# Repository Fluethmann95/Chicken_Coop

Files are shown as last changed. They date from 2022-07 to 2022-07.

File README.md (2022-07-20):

# Hühnerklappensteuerung

- Vollautomatische Steuerung für Stalltüren
- Möglichkeit der Ansteuerung über verschiedene Wege:
	- Am Gerät einstellbarer Zeit für Öffnen und Schließen
	- Helligkeit über externen Sensor
	- Handbetrieb per Drucktaster
- Einstellbare Fahrtzeit in 1/10 Sekunden
- Einstellbare Uhrzeit
- Anschluss für User-Button und Poti
- Diagnose und Konfiguration über LCD und RGB-LED
- 2 Anschlussmöglichkeiten für PNP/NPN Endstops
- Automatische Zeitsynchronisation bei Upload mit PC Zeit
- Update des Codes über SD Karte

##Technische Details
- Arduino MKRZERO µC-Board
- Zeitmessung über DS3231 RTC
- Solar Laderegler mit automatisch geregelter Ladespannung
- PWM Motorausgang mit Strommessung und H-Brücke
- Batteriemanagement

##Aktuelle Konfiguration
- Fahrtdauer 250 s/10
- Öffnen 5:20 Uhr
- Schließen 22:10 Uhr

##Benötigtes Material
- Steuerungsplatine inkl passendem Gehäuse (RND-455 00265)
- Elektromotor 12V mit passendem Getriebe und Seilrolle
- Solarpanel 12V 20Wmax.
- Bleigelbatterie ~10Ah

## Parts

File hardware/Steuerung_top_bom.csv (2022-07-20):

Comment | Designator | Footprint | LCSC Part #
0R | R27 R28 | R0805
1 85A / 250013 | F1 | SMD2920
1 85A / 250013 | F2 | SMD2920
1R 1206 | R26 | R1206W
1µF/16V 140049 | C2 C3 C4 C5 C6 C7 C10 C14 C18 C19 | C0805
10k 120004 | R2 R3 R4 R5 R6 R7 R8 R9 R12 R13 R14 R15 R16 R17 R18 R19 R20 R21 R22 R23 R24 R25 R31 | R0805
15R 120096 | R1 | R0805
100nF/50V 140000 | C1 C8 C9 C11 C12 C13 C15 C16 C20 | C0805
BCX55-10 170000 | T1 T2 T3 T4 T5 | SOT89-BCE
FDS6630 170040 | Q1 | SO08
INA219BIDR | IC2 | SOIC127P600X175-8N
LD1117S50 200345 | IC3 | SPANNUNGSREGLER_SOT-223
MBRS360T3 160013 | D1 | ROLF_SMC
TS4148RY 160030 | D2 | R1206
Tactile Button - SMD (6mm) | S1 | TACTILE_SWITCH_SMD
WS2812B5050 | LED2 LED3 | WS2812B
tba | R10 R11 R32 | R0805

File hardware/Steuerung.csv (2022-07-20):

Qty | Value | Device | Package | Parts | Description
1 |  | B3SN-3X12 | B3SN-3X12_SMD | S1
2 |  | LEDCHIP-LED0805 | CHIP-LED0805 | LED4, LED5 | LED
1 |  | PINHD-1X10 | 1X10 | JP3 | PIN HEADER
2 | 0R | R-EU_R0805 | R0805 | R27, R28 | RESISTOR, European symbol
2 | 1,85A / 250013 | SMD_POLY_2920 | SMD2920 | F1, F2
11 | 100nF/50V 140000 | C-EUC0805 | C0805 | C1, C8, C9, C11, C12, C13, C15, C16, C20, C28, C30 | CAPACITOR, European symbol
4 | 100µF/35V 140086 | RCL_CPOL_E(CASE-D)-100UF/35V | RCL_CE_D | C23, C24, C25, C26 | Kondensatoren, gepolt
14 | 10k 120004 | R-EU_R0805 | R0805 | R2, R4, R6, R9, R12, R16, R19, R20, R23, R24, R25, R29, R30, R31 | RESISTOR, European symbol
1 | 15R 120096 | R-EU_R0805 | R0805 | R1 | RESISTOR, European symbol
3 | 1R 1206 120092 | R-EU_R1206W | R1206W | R26, R33, R34 | RESISTOR, European symbol
10 | 1k 120015 | R-EU_R0805 | R0805 | R3, R5, R7, R8, R14, R15, R17, R18, R21, R22 | RESISTOR, European symbol
14 | 1µF/16V 140049 | C-EUC0805 | C0805 | C2, C3, C4, C5, C6, C7, C10, C14, C18, C19, C21, C22, C27, C29 | CAPACITOR, European symbol
1 | 330R 120024 | R-EU_R0805 | R0805 | R13 | RESISTOR, European symbol
5 | BCX55-10 170000 | BCX55-NPN-SOT89-BCE | SOT89-BCE | T1, T2, T3, T4, T5 | NPN Transistror
2 | CONNECTORS_JST-4 | CONNECTORS_JST-4 | CONNECTORS_EXH_PRN_H_INV | J1, J2 | 4 pin JST connector
1 | DOGS12W-6 | DOGS102-6 | DOGS_LCD_102X64 | LCD1 | EADOGS102-6 mit Hintergrundbeleuchtung EA LED39X41-A
1 | FDS6630 170040 | MOSFET-NCH-FDS6630A | SO08 | Q1 | N-channel MOSFETs
1 | G8ND | RELAYS_OMRON_G8ND2 | RELAYS_OMRON_G8ND2 | K1 | OMRON relay
2 | I2C_Brücke | JP1E | JP1 | JP1, JP2 | JUMPER
1 | INA219BIDR | INA219BIDR | SOIC127P600X175-8N | IC2 | 26-V, Bidirectional, Zero-Drift, High-Side, I2C Out Current/Power Monitor
1 | LD1117S50 200345 | SPANNUNGSREGLER_LD1117S50 | SPANNUNGSREGLER_SOT-223 | IC3
1 | LED39x41 | LED39X41 | LED39X41 | LED1
1 | LM317L | LM317L | TO220L | LM317 | LM317: Adjustable voltage regulator
1 | LM358D | LM358D | SO08 | IC4 | OP AMP also LM158; LM258; LM2904
3 | MBRS360T3 160013 | ROLF_MBRS360T3 | ROLF_SMC | D1, D5, D6
1 | MCP4725 | MCP4725SOT-23 | SOT23-6 | U1 | MCP4725 DAC
1 | MIC2514YM5-TR | MIC2514YM5-TR | SOT95P280X130-5N | S2 | MICROCHIP - MIC2514YM5-TR - IC, SWITCH, HIGH SIDE, TTL INPUT
4 | MKDSN1,5/2-5,08 | MKDSN1,5/2-5,08 | MKDSN1,5/2-5,08 | X1, X2, X3, X6 | MKDSN 1,5/ 2-5,08 Printklemme
2 | MKDSN1,5/3-5,08 | MKDSN1,5/3-5,08 | MKDSN1,5/3-5,08 | X4, X5 | MKDSN 1,5/ 3-5,08 Printklemme
1 | MKR ZERO | MKR_ZERO | MKR_ZERO | IC1
1 | RTC-DS3231-AT24C32 | RTC-DS3231-AT24C32 | RTC-DS3231-AT24C32 | U$3 | RTC Module with Battery and EEPROM based on DS3231 and AT24C32 chips
1 | SMCJ36A 160037 | SMCJ36CA | SMC | D9
1 | SWITCH-ALPS_EC12E_SW | SWITCH-ALPS_EC12E_SW | SWITCH-ALPS_ALPS_EC12E_SW | SW1 | ALPS rotary Encoder EC12E series with switch
5 | TS4148RY 160030 | TS4148RY | R1206 | D2, D3, D4, D7, D8
1 | VA-1224S | VA-1224S | 4SIL | DC1 | DC DC Converter Single Output, 1 Watt
2 | WS2812B5050 | WS2812B5050 | WS2812B | LED2, LED3
4 | n.b. | R-EU_R0805 | R0805 | R38, R39, R45, R46 | RESISTOR, European symbol
1 | nb 0805 | C-EUC0805 | C0805 | C17 | CAPACITOR, European symbol
1 | tba | R-EU_0207/7 | 0207/7 | R35 | RESISTOR, European symbol
10 | tba | R-EU_R0805 | R0805 | R10, R11, R32, R36, R37, R40, R41, R42, R43, R44 | RESISTOR, European symbol

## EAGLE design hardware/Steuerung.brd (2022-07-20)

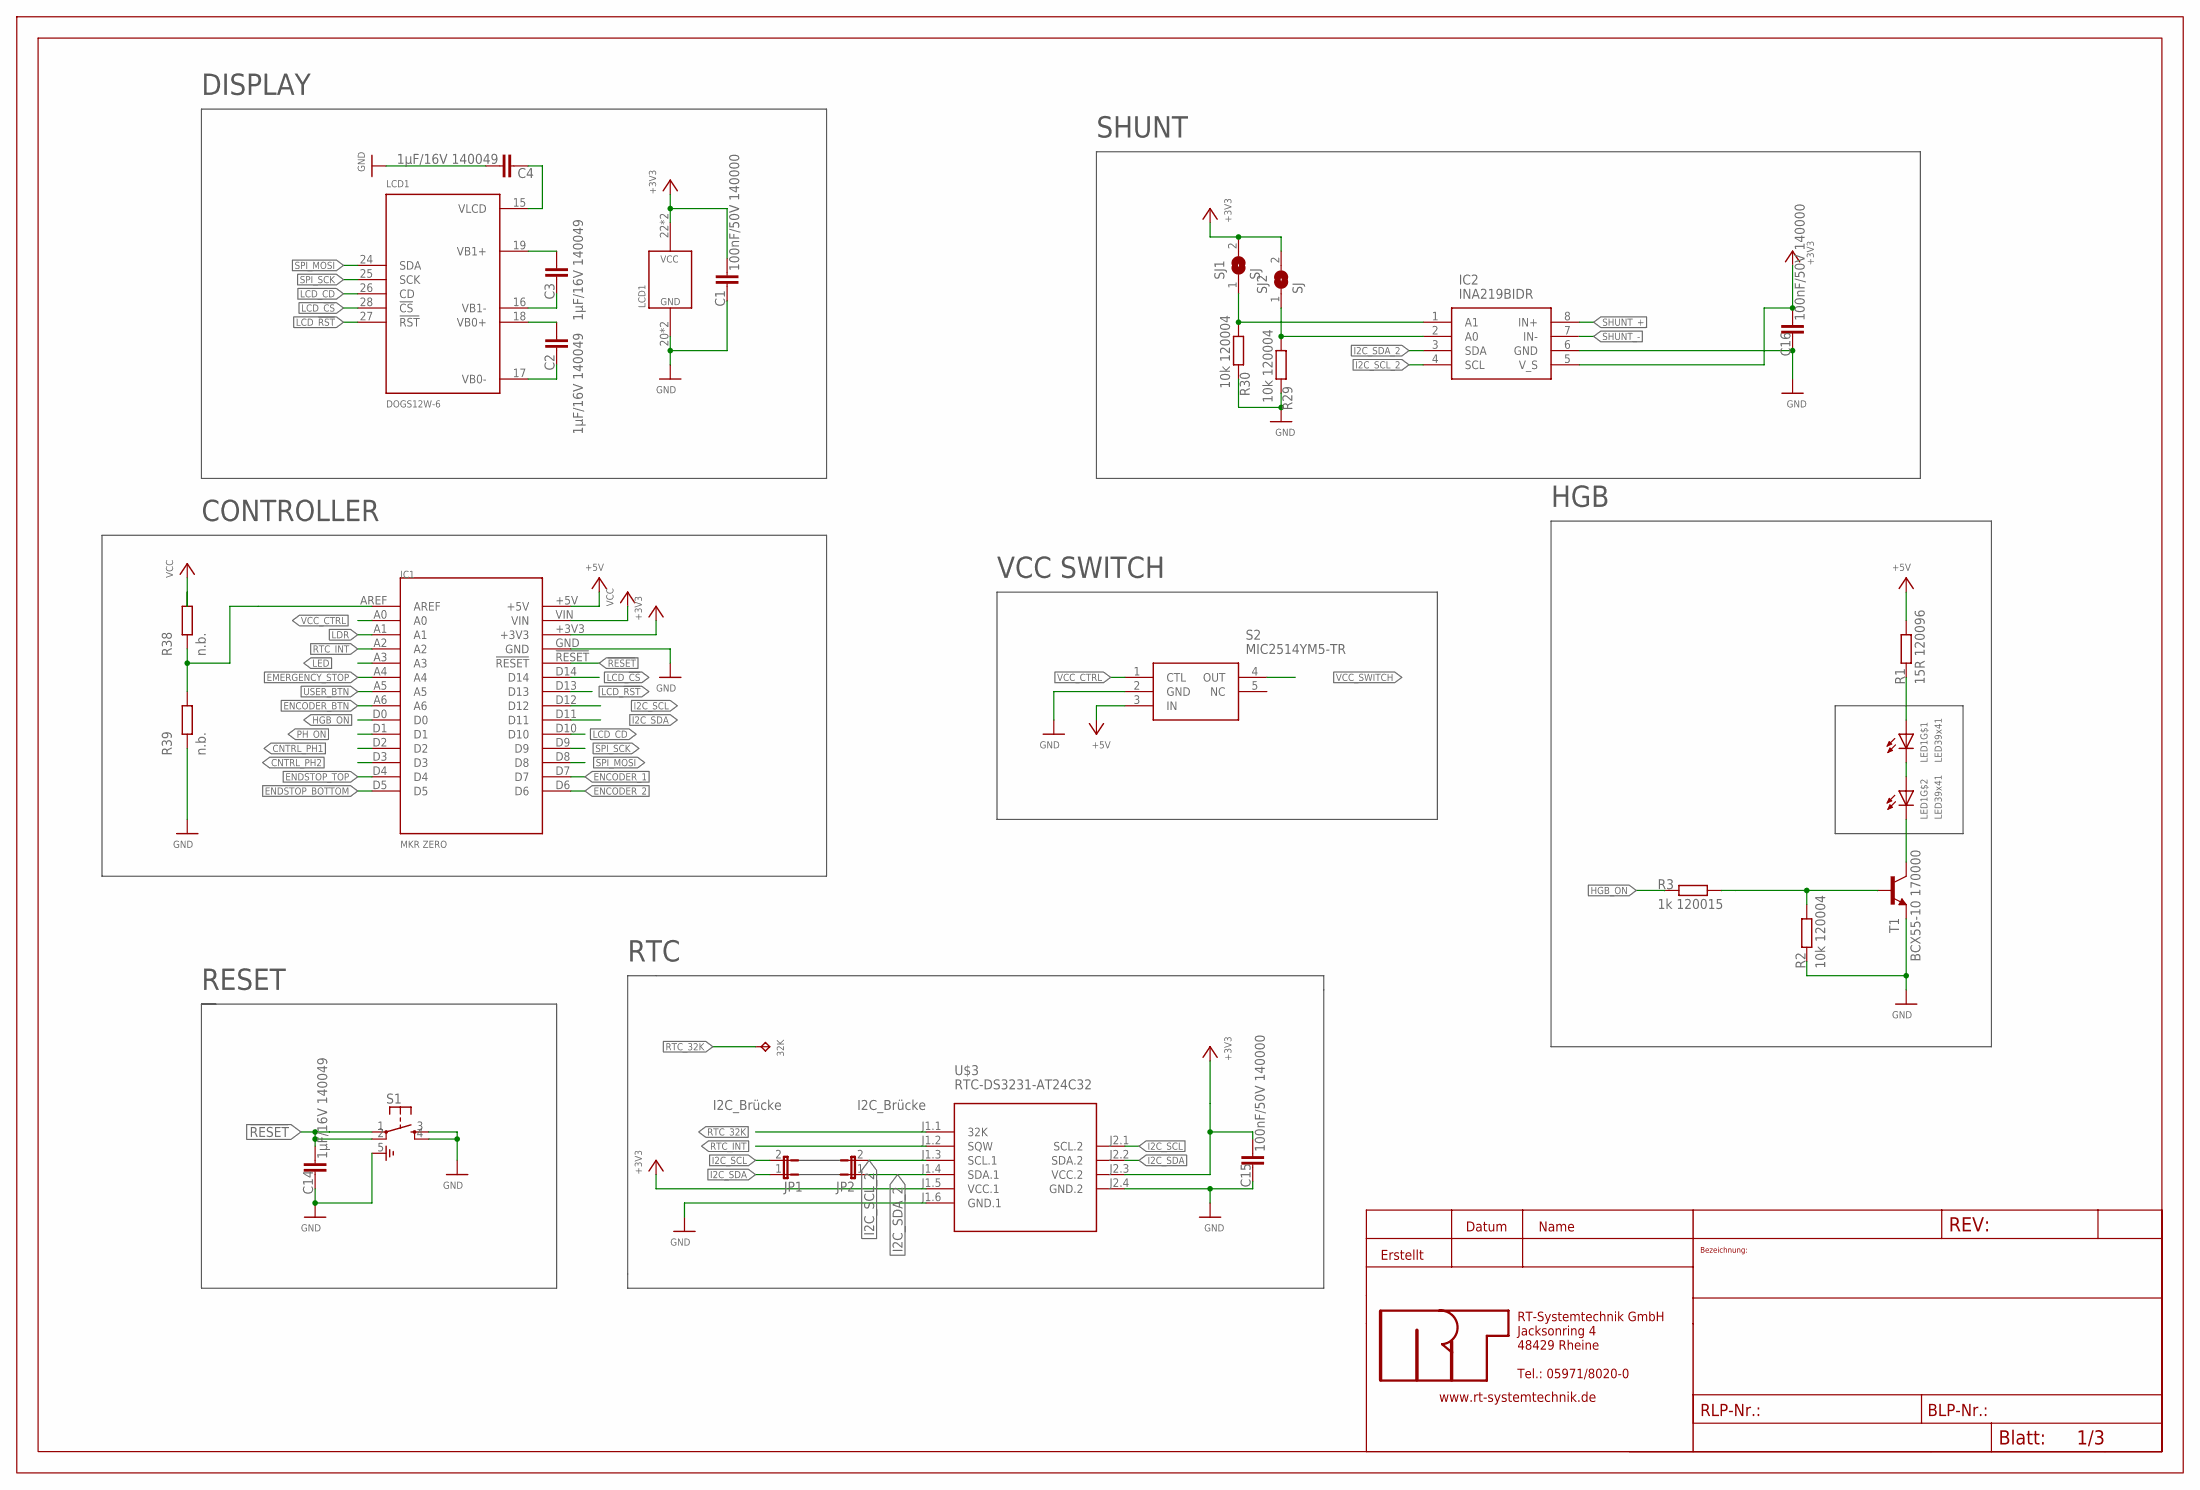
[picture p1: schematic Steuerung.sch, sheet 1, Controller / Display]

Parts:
32K: PAD_SMD_2,5X1; SMD_2,5X1
C1, C15, C16: 100nF/50V 140000; C0805
C2, C3, C4, C14: 1µF/16V 140049; C0805
FRAME1: A3L-LOC; DOKUDATA
IC1: MKR ZERO; MKR_ZERO
IC2: INA219BIDR; SOIC127P600X175-8N
JP1, JP2: I2C_Brücke; JP1
LCD1: DOGS12W-6; DOGS_LCD_102X64
LED1: LED39x41; LED39X41
R1: 15R 120096; R0805
R2, R29, R30: 10k 120004; R0805
R3: 1k 120015; R0805
R38, R39: n.b.; R0805
S1: B3SN-3X12; B3SN-3X12_SMD
S2: MIC2514YM5-TR; SOT95P280X130-5N
SJ1, SJ2: SJ
T1: BCX55-10 170000; SOT89-BCE
U$3: RTC-DS3231-AT24C32

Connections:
!RESET: C14.1, IC1.!RESET, S1.1, S1.2 (P1)
+3V3: C1.1, C15.1, C16.1, IC1.+3V3, IC2.5 (V_S), LCD1.22 (VCC), LCD1.23 (VCC), SJ1.2, SJ2.2, U$3.J1.5 (VCC.1), U$3.J2.3 (VCC.2); also elsewhere on the board
+5V: IC1.+5V, R1.1, S2.3 (IN); also elsewhere on the board
CNTRL_PH1: IC1.D2; also elsewhere on the board
CNTRL_PH2: IC1.D3; also elsewhere on the board
EMERGENCY_STOP: IC1.A4; also elsewhere on the board
ENCODER_1: IC1.D7; also elsewhere on the board
ENCODER_2: IC1.D6; also elsewhere on the board
ENCODER_BTN: IC1.A6; also elsewhere on the board
ENDSTOP_BOTTOM: IC1.D5; also elsewhere on the board
ENDSTOP_TOP: IC1.D4; also elsewhere on the board
GND: C1.2, C4.1, C14.2, C15.2, C16.2, IC1.GND, IC2.6 (GND), LCD1.20 (GND), LCD1.21 (GND), R2.2, R29.1, R30.1, R39.2, S1.3 (S), S1.4 (S1), S1.5, S2.2 (GND), T1.E, U$3.J1.6 (GND.1), U$3.J2.4 (GND.2); also elsewhere on the board
HGB_ON: IC1.D0, R3.2
I2C_SCL: IC1.D12, JP1.2, U$3.J2.1 (SCL.2); also elsewhere on the board
I2C_SCL_2: IC2.4 (SCL), JP2.2, U$3.J1.3 (SCL.1)
I2C_SDA: IC1.D11, JP1.1, U$3.J2.2 (SDA.2); also elsewhere on the board
I2C_SDA_2: IC2.3 (SDA), JP2.1, U$3.J1.4 (SDA.1)
LCD_!CS: IC1.D14, LCD1.28 (!CS)
LCD_!RST: IC1.D13, LCD1.27 (!RST)
LCD_CD: IC1.D10, LCD1.26 (CD)
LDR: IC1.A1; also elsewhere on the board
LED: IC1.A3; also elsewhere on the board
unnamed: C3.1, LCD1.19 (VB1+)
unnamed: C3.2, LCD1.16 (VB1-)
unnamed: C2.1, LCD1.18 (VB0+)
unnamed: C2.2, LCD1.17 (VB0-)
unnamed: C4.2, LCD1.15 (VLCD)
unnamed: LED1.2 (C), LED1.14 (A)
unnamed: LED1.1 (A), R1.2
unnamed: LED1.13 (C), T1.C
unnamed: R2.1, R3.1, T1.B
unnamed: IC2.1 (A1), R30.2, SJ1.1
unnamed: IC2.2 (A0), R29.2, SJ2.1
unnamed: IC1.AREF, R38.2, R39.1
PH_ON: IC1.D1; also elsewhere on the board
RTC_32K: 32K.PIN1, U$3.J1.1 (32K)
RTC_INT: IC1.A2, U$3.J1.2 (SQW)
SHUNT_+: IC2.8 (IN+); also elsewhere on the board
SHUNT_-: IC2.7 (IN-); also elsewhere on the board
SPI_MOSI: IC1.D8, LCD1.24 (SDA)
SPI_SCK: IC1.D9, LCD1.25 (SCK)
USER_BTN: IC1.A5; also elsewhere on the board
VCC: IC1.VIN, R38.1; also elsewhere on the board
VCC_CTRL: IC1.A0, S2.1 (CTL)
VCC_SWITCH: S2.4 (OUT); also elsewhere on the board

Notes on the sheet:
HGB
SHUNT
DISPLAY
CONTROLLER
RESET
RTC
VCC SWITCH

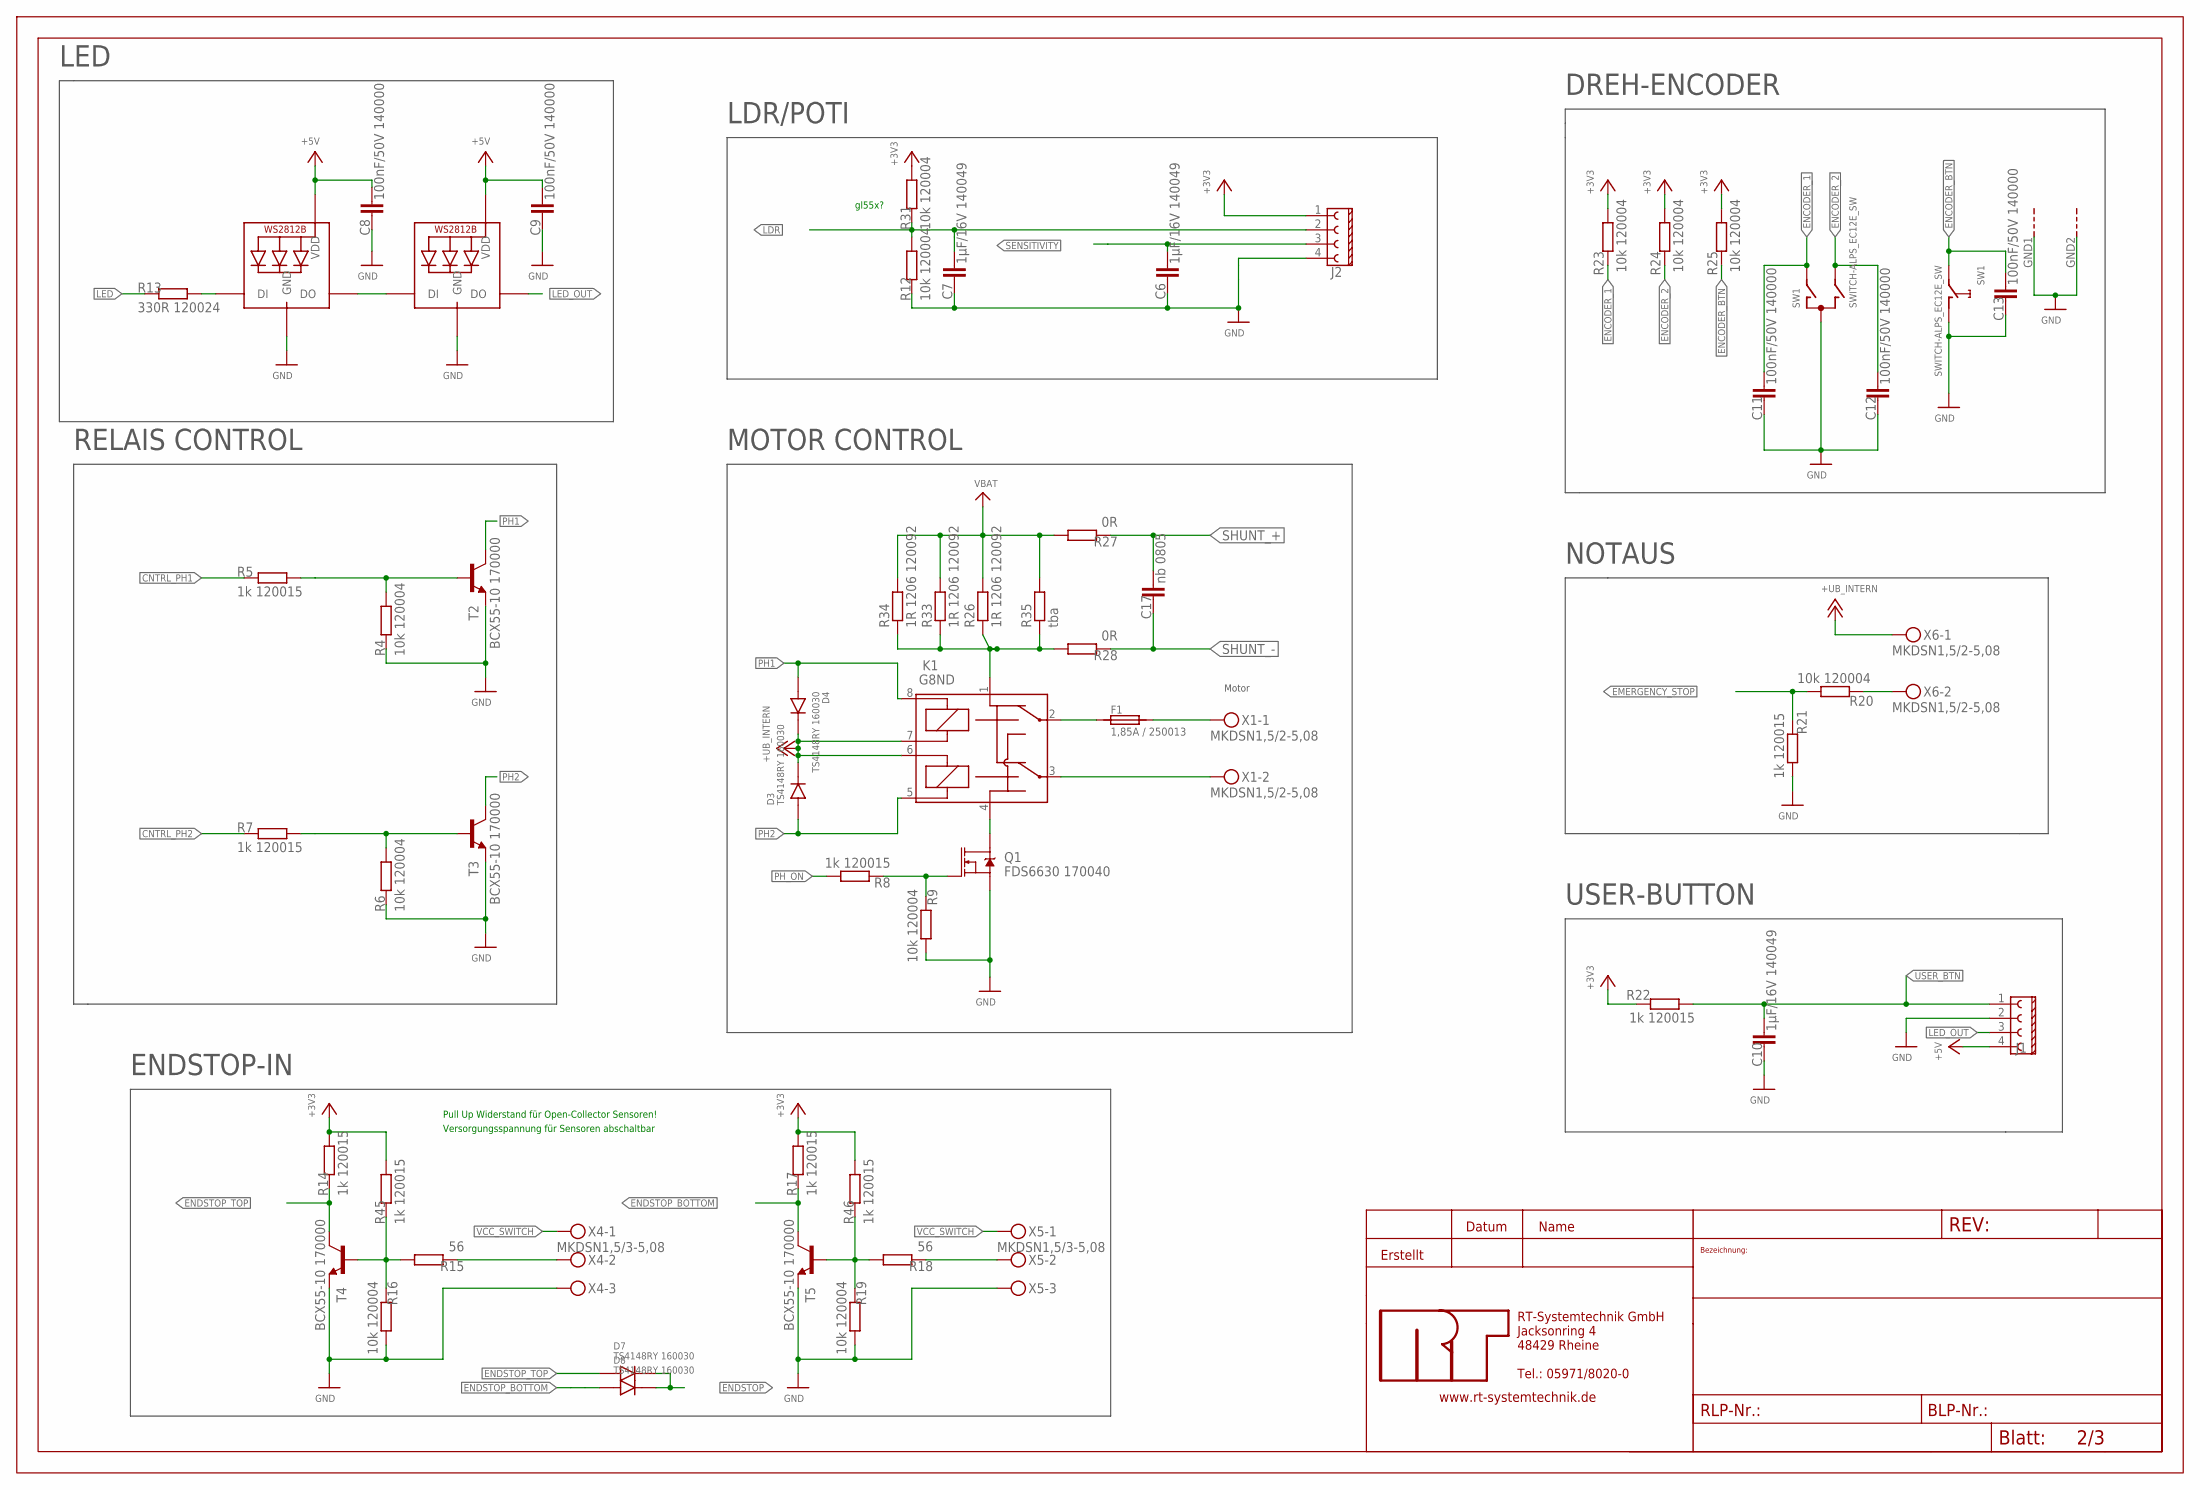
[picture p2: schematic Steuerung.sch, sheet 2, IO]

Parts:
C6, C7, C10: 1µF/16V 140049; C0805
C8, C9, C11, C12, C13: 100nF/50V 140000; C0805
C17: nb 0805; C0805
D3, D4, D7, D8: TS4148RY 160030; R1206
F1: 1,85A / 250013; SMD2920
FRAME2: A3L-LOC; DOKUDATA
J1, J2: CONNECTORS_JST-4; CONNECTORS_EXH_PRN_H_INV
K1: G8ND; RELAYS_OMRON_G8ND2
LED2, LED3: WS2812B5050; WS2812B
Q1: FDS6630 170040; SO08
R4, R6, R9, R12, R16, R19, R20, R23, R24, R25, R31: 10k 120004; R0805
R5, R7, R8, R14, R17, R21, R22, R45, R46: 1k 120015; R0805
R13: 330R 120024; R0805
R15, R18: 56; R0805
R26, R33, R34: 1R 1206 120092; R1206W
R27, R28: 0R; R0805
R35: tba; 0207/7
SW1: SWITCH-ALPS_EC12E_SW; SWITCH-ALPS_ALPS_EC12E_SW
T2, T3, T4, T5: BCX55-10 170000; SOT89-BCE
X1, X6: MKDSN1,5/2-5,08
X4, X5: MKDSN1,5/3-5,08

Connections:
+3V3: J2.1, R14.1, R17.1, R22.2, R23.1, R24.1, R25.1, R31.1, R45.1, R46.1; also elsewhere on the board
+5V: C8.1, C9.1, J1.4, LED2.1-VDD (VDD), LED3.1-VDD (VDD); also elsewhere on the board
+UB_INTERN: D3.2 (C), D4.2 (C), K1.6 (2SA), K1.7 (1SB), X6.1; also elsewhere on the board
CNTRL_PH1: R5.2; also elsewhere on the board
CNTRL_PH2: R7.2; also elsewhere on the board
EMERGENCY_STOP: R20.1, R21.2; also elsewhere on the board
ENCODER_1: C11.1, R23.2, SW1.A; also elsewhere on the board
ENCODER_2: C12.1, R24.2, SW1.B; also elsewhere on the board
ENCODER_BTN: C13.1, R25.2, SW1.E (2); also elsewhere on the board
ENDSTOP: D7.2 (C), D8.2 (C); also elsewhere on the board
ENDSTOP_BOTTOM: D8.1 (A), R17.2, T5.C; also elsewhere on the board
ENDSTOP_TOP: D7.1 (A), R14.2, T4.C; also elsewhere on the board
GND: C6.2, C7.2, C8.2, C9.2, C10.2, C11.2, C12.2, C13.2, J1.2, J2.4, LED2.3-GND (GND), LED3.3-GND (GND), Q1.1 (S), Q1.2 (S), Q1.3 (S), R4.2, R6.2, R9.1, R12.2, R16.1, R19.1, R21.1, SW1.C, SW1.D (1), SW1.GND1 (G), SW1.GND2 (G), T2.E, T3.E, T4.E, T5.E, X4.3, X5.3; also elsewhere on the board
LDR: C7.1, J2.2, R12.1, R31.2; also elsewhere on the board
LED: R13.2; also elsewhere on the board
LED_OUT: J1.3, LED3.2-DOUT (DO)
unnamed: K1.4 (O2), Q1.5 (D), Q1.6 (D), Q1.7 (D), Q1.8 (D)
unnamed: Q1.4 (G), R8.2, R9.2
unnamed: R4.1, R5.1, T2.B
unnamed: R6.1, R7.1, T3.B
unnamed: K1.3 (P2), X1.2
unnamed: F1.1, K1.2 (P1)
unnamed: F1.2, X1.1
unnamed: LED2.4-DIN (DI), R13.1
unnamed: LED2.2-DOUT (DO), LED3.4-DIN (DI)
unnamed: R15.1, R16.2, R45.2, T4.B
unnamed: R15.2, X4.2
unnamed: R18.1, R19.2, R46.2, T5.B
unnamed: R18.2, X5.2
unnamed: K1.1 (O1), R26.1, R28.1, R33.1, R34.1, R35.1
unnamed: R20.2, X6.2
PH1: D4.1 (A), K1.8 (1SA), T2.C
PH2: D3.1 (A), K1.5 (2SB), T3.C
PH_ON: R8.1; also elsewhere on the board
SENSITIVITY: C6.1, J2.3; also elsewhere on the board
SHUNT_+: C17.1, R27.2; also elsewhere on the board
SHUNT_-: C17.2, R28.2; also elsewhere on the board
USER_BTN: C10.1, J1.1, R22.1; also elsewhere on the board
VBAT: R26.2, R27.1, R33.2, R34.2, R35.2; also elsewhere on the board
VCC_SWITCH: X4.1, X5.1; also elsewhere on the board

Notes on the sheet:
Motor
gl55x?
LED
LDR/POTI
DREH-ENCODER
NOTAUS
MOTOR CONTROL
RELAIS CONTROL
ENDSTOP-IN
USER-BUTTON
Pull Up Widerstand für Open-Collector Sensoren!
Versorgungsspannung für Sensoren abschaltbar

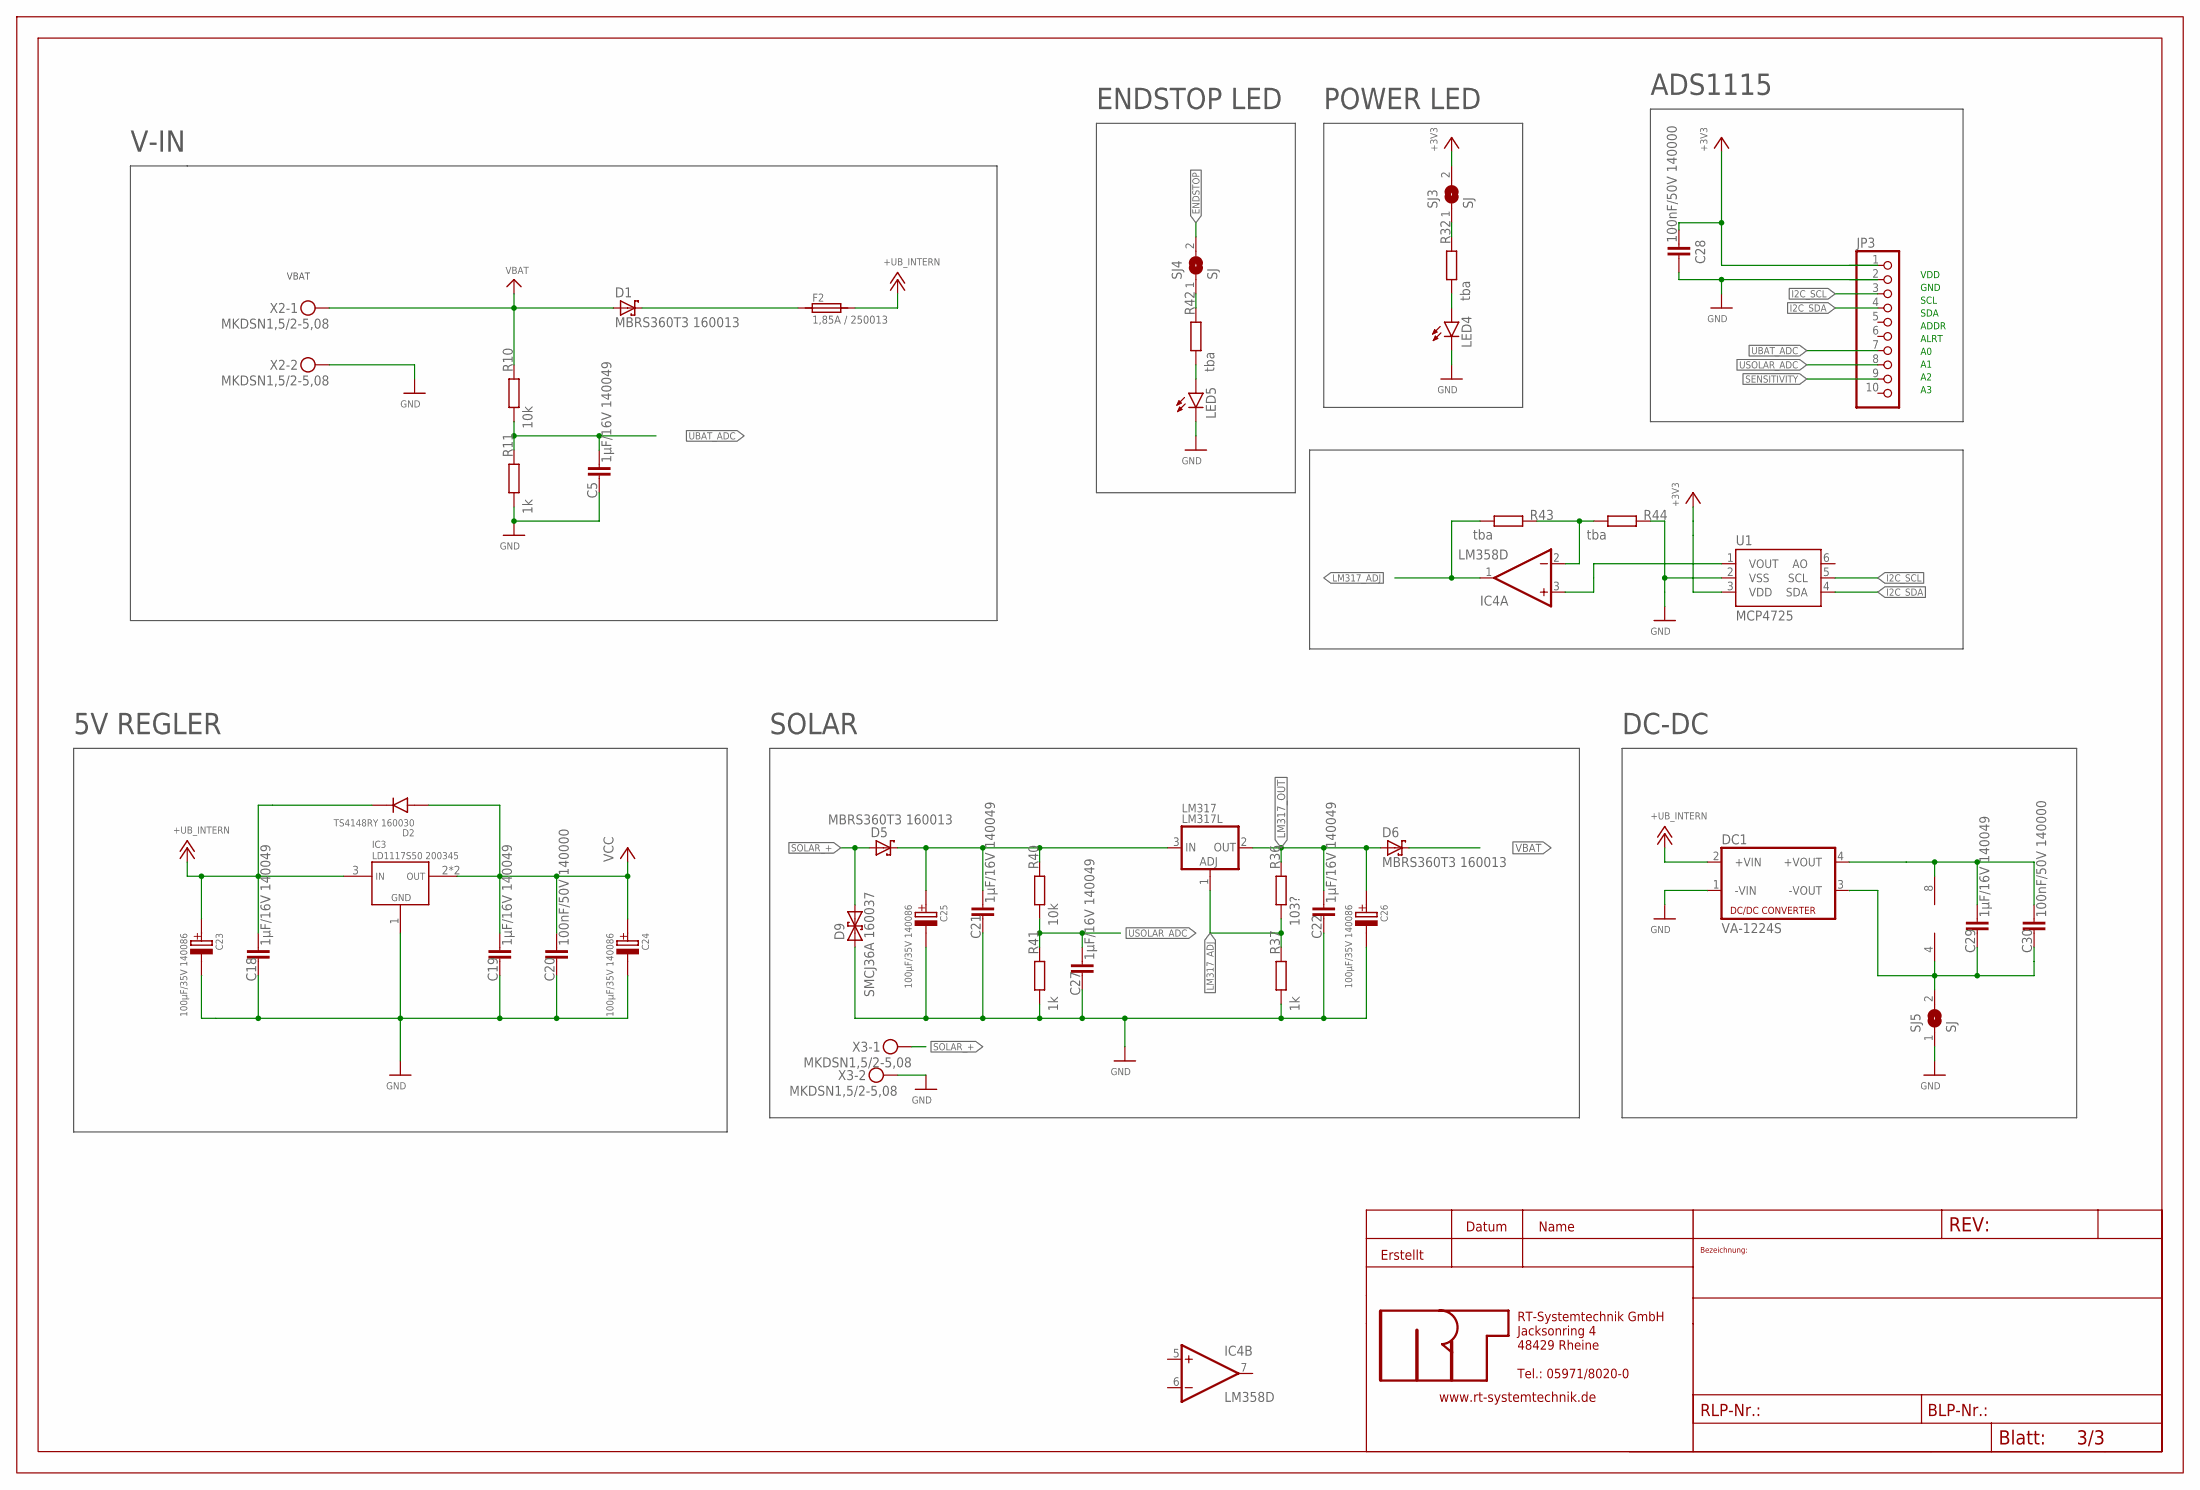
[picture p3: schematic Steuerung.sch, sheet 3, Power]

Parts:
C5, C18, C19, C21, C22, C27, C29: 1µF/16V 140049; C0805
C20, C28, C30: 100nF/50V 140000; C0805
C23, C24, C25, C26: 100µF/35V 140086; RCL_CE_D
D1, D5, D6: MBRS360T3 160013; ROLF_SMC
D2: TS4148RY 160030; R1206
D9: SMCJ36A 160037; SMC
DC1: VA-1224S; 4SIL
F2: 1,85A / 250013; SMD2920
FRAME3: A3L-LOC; DOKUDATA
IC3: LD1117S50 200345; SPANNUNGSREGLER_SOT-223
IC4: LM358D; SO08
JP3: PINHD-1X10; 1X10
LED4, LED5: LEDCHIP-LED0805; CHIP-LED0805
LM317: LM317L; TO220L
R10, R40: 10k; R0805
R11, R37, R41: 1k; R0805
R32, R42, R43, R44: tba; R0805
R36: 103?; R0805
SJ3, SJ4, SJ5: SJ
U1: MCP4725; SOT23-6
X2, X3: MKDSN1,5/2-5,08

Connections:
+3V3: C28.1, JP3.1, SJ3.2, U1.3 (VDD); also elsewhere on the board
+UB_INTERN: C18.1, C23.+, D2.2 (C), DC1.2 (+VIN), F2.2, IC3.3 (IN); also elsewhere on the board
ENDSTOP: SJ4.2; also elsewhere on the board
GND: C5.2, C18.2, C19.2, C20.2, C21.2, C22.2, C23.-, C24.-, C25.-, C26.-, C27.2, C28.2, D9.A (1), DC1.1 (-VIN), IC3.1 (GND), JP3.2, LED4.C, LED5.C, R11.2, R37.2, R41.2, R44.1, U1.2 (VSS), X2.2, X3.2; also elsewhere on the board
I2C_SCL: JP3.3, U1.5 (SCL); also elsewhere on the board
I2C_SDA: JP3.4, U1.4 (SDA); also elsewhere on the board
LM317_ADJ: IC4.1 (OUT), LM317.1 (ADJ), R36.2, R37.1, R43.2
LM317_OUT: C22.1, C26.+, D6.A, LM317.2 (OUT), R36.1
unnamed: D1.K, F2.1
unnamed: LED4.A, R32.2
unnamed: C21.1, C25.+, D5.K, LM317.3 (IN), R40.1
unnamed: R32.1, SJ3.1
unnamed: IC4.3 (+IN), U1.1 (VOUT)
unnamed: LED5.A, R42.2
unnamed: R42.1, SJ4.1
unnamed: C29.1, C30.1, DC1.4 (+VOUT), IC4.8 (V+)
unnamed: IC4.2 (-IN), R43.1, R44.2
unnamed: C29.2, C30.2, DC1.3 (-VOUT), IC4.4 (V-), SJ5.2
SENSITIVITY: JP3.9; also elsewhere on the board
SOLAR_+: D5.A, D9.C (2), X3.1
UBAT_ADC: C5.1, JP3.7, R10.2, R11.1
USOLAR_ADC: C27.1, JP3.8, R40.2, R41.1
VBAT: D1.A, D6.K, R10.1, X2.1; also elsewhere on the board
VCC: C19.1, C20.1, C24.+, D2.1 (A), IC3.2 (OUT), IC3.4 (OUT); also elsewhere on the board

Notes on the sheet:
VBAT
5V REGLER
V-IN
SOLAR
POWER LED
VDD GND SCL SDA ADDR ALRT A0 A1 A2 A3
ENDSTOP LED
ADS1115
DC-DC

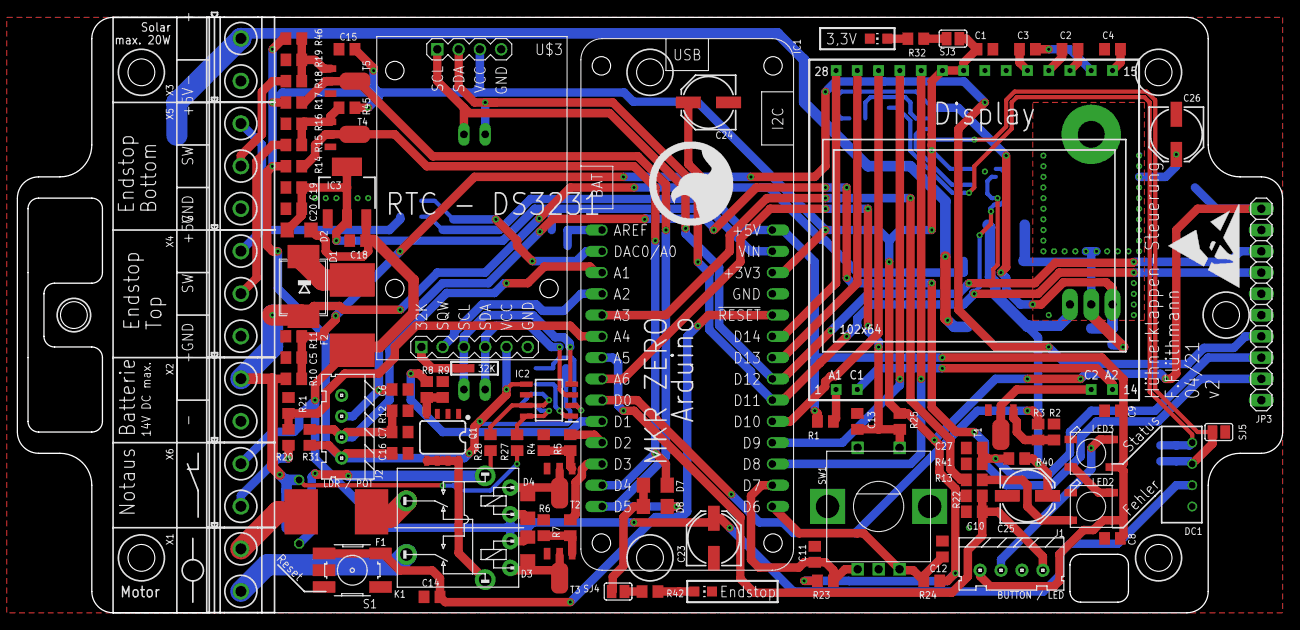
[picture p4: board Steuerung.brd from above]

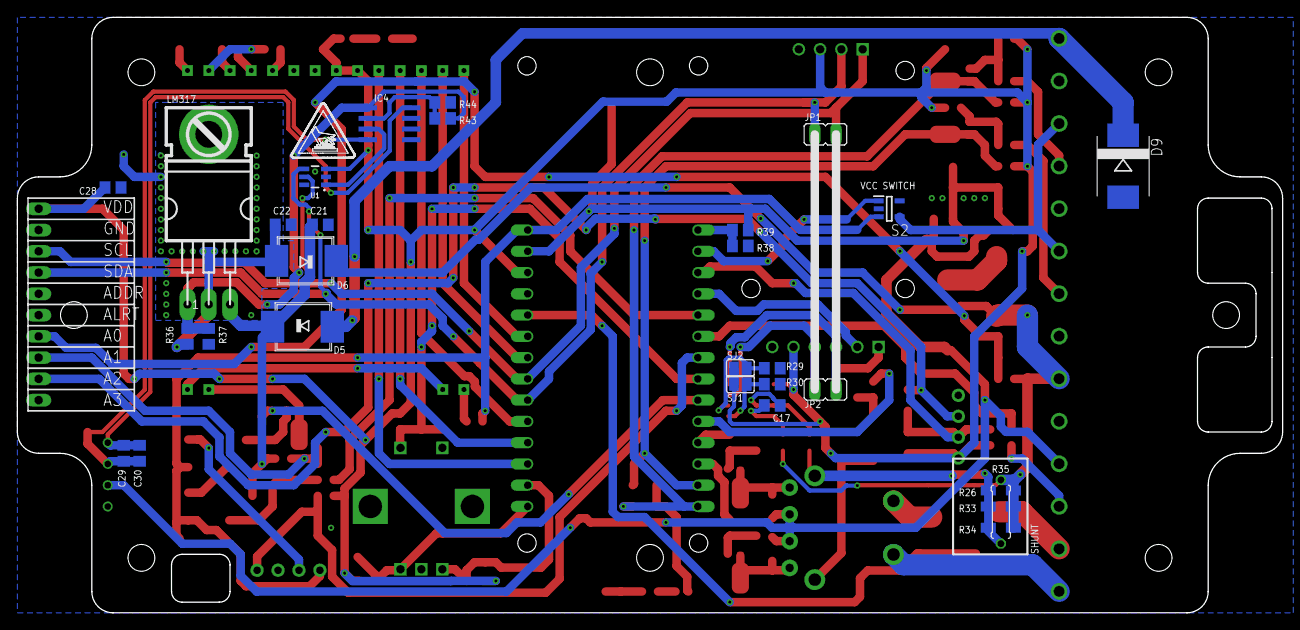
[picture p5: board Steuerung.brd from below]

Board: 2 copper layers, 151.1 x 71.1 mm, 133 parts (29 on the bottom side), 82 nets.

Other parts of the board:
U$4: ESD_10.00
U$5: CS-2016-LOGO-10MM

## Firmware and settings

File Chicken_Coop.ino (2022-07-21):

//LED
#include <Adafruit_NeoPixel.h>

//Encoder
#include <Encoder.h>

//Display
#include <DogGraphicDisplay.h>
#include "ubuntumono_b_16.h" //Schriftart 16p
#include "ubuntumono_b_8.h" //Schriftart 8p
#include "font_6x8.h"

//RTC
#include <DS3231.h>
#include <Wire.h>

//Arduino
#include <FlashStorage.h>
#include <ArduinoLowPower.h>

//Stromsensor
#include <Adafruit_INA219.h>

//ADC
#include<ADS1115_WE.h>

//DAC
#include <stdio.h>
#include <stdlib.h>
#include "MCP4725.h"

//RTC EEPROM
#include <AT24Cxx.h>
//  eep.update(address, val); address = speicherbank, value = wert (byte!)
//  value = eep.read(address);

//SD Update
#include <SDU.h>



//Defines
#define HGB_ON 0          //Ansteuerung Display Hintergrundbeleuchtung HIGH Aktiv -OUT PWM
#define PH_ON 1           //PWM Ansteuerung Motorphase HIGH Aktiv -OUT PWM
#define CNTRL_PH1 2       //Umschaltung Anschluss X1-1 HIGH Aktiv -OUT
#define CNTRL_PH2 3       //Umschaltung Anschluss X1-2 HIGH Aktiv -OUT
#define ENDSTOP_TOP 4     //Anschluss X4 HIGH Aktiv -IN
#define ENDSTOP_BOTTOM 5  //Anschluss X5 HIGH Aktiv -IN
#define ENCODER_2 6       //Drehencoder -IN LIB
#define ENCODER_1 7       //Drehencoder -IN LIB
#define SPI_MOSI 8        //SPI BUS MOSI LIB
#define SPI_SCK 9         //SPI BUS SCK LIB
#define LCD_CD 10         //Umschaltung Command<->Data Display -OUT LIB
#define I2C_SDA 11        //I2C BUS Data LIB
#define I2C_SCL 12        //I2C BUS Clock LIB
#define LCD_RST 13        //LCD Reset -OUT LIB
#define LCD_CS 14         //SPI BUS Chip Select LCD -OUT LIB
#define VCC_CTRL A0       //Schalten der Endstop-Versorgungsspannung HIGH Aktiv -OUT
#define LDR A1            //Erkennung Helligkeit über LDR -IN ANALOG
#define RTC_INT A2        //Programmierbarer Interrupt der RTC -IN
#define LED_PIN A3        //WS2812 Ausgang -OUT LIB
#define NOTAUS A4         //NOTAUS Eingang LOW Aktiv -IN
#define USER_BTN A5       //User Taster Eingang LOW Aktiv -IN
#define ENCODER_BTN A6    //Button des Drehencoders LOW Aktiv Interner Pullup -IN



//Board LED
#define LED_COUNT 2 //Anzahl der angeschlossenen LEDS, default = 2
Adafruit_NeoPixel LED(LED_COUNT, LED_PIN, NEO_GRB + NEO_KHZ800);

//Encoder
Encoder Drehencoder(6, 7);
long EncodersetPosition = 0;
long EncodernewPosition = 0;
long EncoderoldPosition = -999;
bool EncoderbtnState = false;
bool EncoderbuttonToggle = false;
bool EncoderbtnLastState = false;
unsigned long lastDebounceTime = 0;  // the last time the output pin was toggled
unsigned long debounceDelay = 50;    // the debounce time; increase if the output flickers

//Button
bool btnState = false;

//Endstops
bool EndstopTop = false;
bool EndstopBottom = false;
bool FallingEdge;
bool lastcheck;

//Poti
int PotiValue = 0;

//LDR
int LDRValue = 0;

//UBAT
int UBATValue = 0;

//NOTAUS
bool NOTAUSstate = false;

//Display
DogGraphicDisplay DOG;
bool displaytimer = true;
unsigned long displaytimeout = 10000; //Nachlaufzeit für die HGB
unsigned long displaytime = 0;

//RTC
DS3231 Uhr;
String CompileTime = __TIME__; //Compile Time / String / "hh:mm:ss"
int CompileHour = 0;
int CompileMinute = 0;
int CompileSecond = 0;

//Temperatur
int temperatur = 0;
int tempcal = -3;

//Flash
typedef struct {
  boolean valid;
  int stundehoch;
  int minutehoch;
  int stunderunter;
  int minuterunter;
  int ontime;
} Daten;
FlashStorage(Flashspeicher, Daten); //Speicherplatz für "Daten" in "Flashspeicher" freihalten
Daten Flashdaten; //Objekt "Flashdaten" aus Klasse "Daten" erzeugen

//INA
Adafruit_INA219 ina219;
float current_mA = 0;

//ADC
#define I2C_ADDRESS 0x48
ADS1115_WE adc = ADS1115_WE(I2C_ADDRESS);
float UBAT = 0; //Channel A0
float USOLAR = 0; //Channel A1
float SENSITIVITY = 0; //Channel A2
//Channel A3 des ADC ist frei

//DAC
MCP4725 MCP(0x60);  // 0x62 or 0x63
long DAC_OUTPUT = 0;

//Zeiteinstellung
int zwischenspeicherStunden = 0;
int zwischenspeicherMinuten = 0;
int zwischenspeicherOnTime  = 0;
int minuteset = 0;
int stundeset = 0;
int zwischenspeicherUhrzeitStunden = 0;
int zwischenspeicherUhrzeitMinuten = 0;

//Relais
bool relaison;
unsigned long currentmillis = 0;

//Loop-Variablen
int minuteold = 0;
int menuposition = 0;
bool menuentered;

//Handbetrieb
int handstate = 0;
bool pressed = false;
bool handbetrieb = false;
static int up_down = 0;

//EEPROM
#define i2c_address 0x57 //RTC EEPROM Adresse
#define EEPROM_SIZE 32 //kbyte


void setup() {
  PIN_INIT();
  LED_INIT();
  SERIAL_INIT();
  DISPLAY_INIT();
  I2C_INIT();
  INA_INIT();
  RTC_INIT();
  ADC_INIT();
  DAC_INIT();
  EEPROM_INIT();
  FlashRead();
  DOG.createCanvas(128, 64, 0, 0);

  setEncoderPosition(menuposition);
}

//Endlosschleife
void loop() {
  while (!ReadEncoder()) {}
  while (!readEncoderBtn()) {}
  while (!readBtn()) {}
  while (!readNOTAUS()) {}
  while (!readEndstopTop()) {}
  while (!readEndstopBottom()) {}
  while (!readPotiValue()) {}
  while (!readLDRValue()) {}
  while (!readUbat()) {}
  while (!readINA()) {}
  while (!HGBTimer()) {}
  while (!readADC()) {}
  while (!checkEdge()) {}

  Menu();
  RelaisOff(Flashdaten.ontime); //Relais nach Erreichen der Zeit abschalten (ms, unsigned long)
  AlarmOff(210); //Ausgänge bei Erreichen des Max. Stroms abschalten (mA, float)
  Solar(); //Laderegler
  Handbetrieb(); //Ablauf Handbetrieb
  UndervoltageCheck();

  if (minuteold != Uhr.getMinute()) { //"Programmdurchlauf" minütlich ausführen
    Programmdurchlauf();
    minuteold = Uhr.getMinute();
  }


}


//Wird minütlich ausgeführt
bool Programmdurchlauf()
{

  bool a, b;

  String hour = String(Uhr.getHour(a, b));
  String minute = String(Uhr.getMinute());
  String Null = "0";
  if (Uhr.getHour(a, b) < 10)
  {
    hour = Null + hour;
  }
  if (Uhr.getMinute() < 10)
  {
    minute = Null + minute;
  }
  String second = String(Uhr.getSecond());
  float UBATFloat = float(UBATValue) * 0.1;
  String UBAT = String(UBATFloat, 1);


  DOG.clear();

  DOG.drawLine(0, 17, 127, 17);
  DOG.string(0, 0, UBUNTUMONO_B_16, (hour + ":" + minute).c_str() , ALIGN_LEFT);
  DOG.string(0, 0, UBUNTUMONO_B_16, (UBAT + "V").c_str(), ALIGN_RIGHT);

  TimeCheck();

  return true;
}


bool Menu ()
{
  if (!EncoderbuttonToggle)
  {
    menuposition = EncodernewPosition;

    if (menuposition < 9 && menuposition >= 0)
    {
      switch (menuposition)
      {
        case 0:
        case 1:
          {
            temperatur = (Uhr.getTemperature() + tempcal);
            String sTemperatur = String(temperatur);
            if (!UndervoltageCheck())
            {
              DOG.string(0, 4, UBUNTUMONO_B_16, ("     " + sTemperatur + " C     ").c_str()  , ALIGN_CENTER);
              DOG.string(0, 6, UBUNTUMONO_B_16, "   Temperatur   ", ALIGN_CENTER);

            }
            else
            {
              DOG.string(0, 6, UBUNTUMONO_B_16, "Akku laden!"  , ALIGN_CENTER);
              DOG.string(0, 4, UBUNTUMONO_B_16, "   WARNUNG!   ", ALIGN_CENTER);

            }

          }
          break;
        case 2:
        case 3:
          { String NullStunde;
            String NullMinute;
            String stunderunter = String(Flashdaten.stunderunter);
            String minuterunter = String(Flashdaten.minuterunter);
            if (Flashdaten.stunderunter < 10)
            {
              NullStunde = "0";
            }
            else
            {
              NullStunde = "";
            }
            if (Flashdaten.minuterunter < 10)
            {
              NullMinute = "0";
            }
            else
            {
              NullMinute = "";
            }
            DOG.string(0, 4, UBUNTUMONO_B_16, ("     " + NullStunde + stunderunter + ":" + NullMinute + minuterunter + " Uhr" + "     ").c_str()  , ALIGN_CENTER);
            DOG.string(0, 6, UBUNTUMONO_B_16, "   Schliessen   ", ALIGN_CENTER);
          }
          break;
        case 4:
        case 5:
          {
            String NullStunde;
            String NullMinute;
            String stundehoch = String(Flashdaten.stundehoch);
            String minutehoch = String(Flashdaten.minutehoch);
            if (Flashdaten.stundehoch < 10)
            {
              NullStunde = "0";
            }
            else
            {
              NullStunde = "";
            }
            if (Flashdaten.minutehoch < 10)
            {
              NullMinute = "0";
            }
            else
            {
              NullMinute = "";
            }
            DOG.string(0, 4, UBUNTUMONO_B_16, ("     " + NullStunde + stundehoch + ":" + NullMinute + minutehoch + " Uhr" + "     ").c_str()  , ALIGN_CENTER);
            DOG.string(0, 6, UBUNTUMONO_B_16, "   Oeffnen   ", ALIGN_CENTER);
          }
          break;
        case 6:
        case 7:
          {
            bool a, b;
            String hour = String(Uhr.getHour(a, b));
            String minute = String(Uhr.getMinute());
            String second = String(Uhr.getSecond());
            String Null = "0";

            if (Uhr.getHour(a, b) < 10)
            {
              hour = Null + hour;
            }
            if (Uhr.getMinute() < 10)
            {
              minute = Null + minute;
            }
            if (Uhr.getSecond() < 10)
            {
              second = Null + second;
            }
            DOG.string(0, 4, UBUNTUMONO_B_16, ("" + hour + ":" + minute + ":" + second + "  Uhr" + "     ").c_str() , ALIGN_LEFT);
            DOG.string(0, 6, UBUNTUMONO_B_16, "   Zeit   ", ALIGN_CENTER);
          }
          break;
        case 8:
        case 9:
          {
            String laufzeit = "     " + String(Flashdaten.ontime) + " s/10" + "     ";
            DOG.string(0, 4, UBUNTUMONO_B_16, laufzeit.c_str(), ALIGN_CENTER);
            DOG.string(0, 6, UBUNTUMONO_B_16, "  Fahrdauer  ", ALIGN_CENTER);
          }
          break;
        default:

          DOG.string(0, 4, UBUNTUMONO_B_16, "   Default   ", ALIGN_CENTER);
          //dürfte nie eintreten!
          break;
      }
    }

    else if (menuposition > 9)
    {
      menuposition = 0;
      setEncoderPosition(menuposition);

    }
    else if (menuposition < 0)
    {
      menuposition = 8;
      setEncoderPosition(menuposition);

    }
  }


  else {
    DOG.string(0, 6, UBUNTUMONO_B_16, "   Set aktiv   ", ALIGN_CENTER);
    if (menuposition < 9 && menuposition >= 0)
    {

      switch (menuposition)
      {
        case 0:
        case 1:
          {
            //Platzhalter
          }
          break;
        case 2:
        case 3:
          {
            String NullStunde;
            String NullMinute;
            if (EncodernewPosition < 60 && EncodernewPosition >= 0)
            { Flashdaten.minuterunter = EncodernewPosition;
            }
            else if (EncodernewPosition > 59)
            {
              setEncoderPosition(0);
              if (Flashdaten.stunderunter < 23 && Flashdaten.stunderunter >= 0)
              {
                Flashdaten.stunderunter = Flashdaten.stunderunter + 1;
              }
              else
              {
                Flashdaten.stunderunter = 0;
              }
            }
            else if (EncodernewPosition < 0)
            {
              setEncoderPosition(58);
              if (Flashdaten.stunderunter < 24 && Flashdaten.stunderunter > 0)
              {
                Flashdaten.stunderunter = Flashdaten.stunderunter - 1;

              }
              else
              {
                Flashdaten.stunderunter = 23;
              }
            }
            if (Flashdaten.stunderunter < 10)
            {
              NullStunde = "0";
            }
            else
            {
              NullStunde = "";
            }
            if (EncodernewPosition < 10)
            {
              NullMinute = "0";
            }
            else
            {
              NullMinute = "";
            }
            String Value = "   " + NullStunde + String(Flashdaten.stunderunter) + ":" + NullMinute + String(EncodernewPosition) + " Uhr" + "   ";

            DOG.string(0, 4, UBUNTUMONO_B_16, Value.c_str() , ALIGN_CENTER);

          }

          break;
        case 4:
        case 5:
          {
            String NullStunde;
            String NullMinute;
            if (EncodernewPosition < 60 && EncodernewPosition >= 0)
            { Flashdaten.minutehoch = EncodernewPosition;
            }
            else if (EncodernewPosition > 59)
            {
              setEncoderPosition(0);
              if (Flashdaten.stundehoch < 23 && Flashdaten.stundehoch >= 0)
              {
                Flashdaten.stundehoch = Flashdaten.stundehoch + 1;
              }
              else
              {
                Flashdaten.stundehoch = 0;
              }
            }
            else if (EncodernewPosition < 0)
            {
              setEncoderPosition(58);
              if (Flashdaten.stundehoch < 24 && Flashdaten.stundehoch > 0)
              {
                Flashdaten.stundehoch = Flashdaten.stundehoch - 1;
              }
              else
              {
                Flashdaten.stundehoch = 23;
              }
            }
            if (Flashdaten.stundehoch < 10)
            {
              NullStunde = "0";
            }
            else
            {
              NullStunde = "";
            }
            if (EncodernewPosition < 10)
            {
              NullMinute = "0";
            }
            else
            {
              NullMinute = "";
            }
            String Value = "   " + NullStunde + String(Flashdaten.stundehoch) + ":" + NullMinute + String(EncodernewPosition) + " Uhr" + "   ";

            DOG.string(0, 4, UBUNTUMONO_B_16, Value.c_str() , ALIGN_CENTER);


          }
          break;
        case 6:
        case 7:
          {
            String NullStunde;
            String NullMinute;

            if (EncodernewPosition < 60 && EncodernewPosition >= 0)
            { minuteset = EncodernewPosition;
            }
            else if (EncodernewPosition > 59)
            {
              setEncoderPosition(0);
              if (stundeset < 23 && stundeset >= 0)
              {
                stundeset = stundeset + 1;
              }
              else
              {
                stundeset = 0;
              }
            }
            else if (EncodernewPosition < 0)
            {
              setEncoderPosition(58);
              if (stundeset < 24 && stundeset > 0)
              {
                stundeset = stundeset - 1;

              }
              else
              {
                stundeset = 23;
              }
            }

            if (stundeset < 10)
            {
              NullStunde = "0";
            }
            else
            {
              NullStunde = "";
            }
            if (EncodernewPosition < 10)
            {
              NullMinute = "0";
            }
            else
            {
              NullMinute = "";
            }
            String Value = "  " + NullStunde + String(stundeset) + ":" + NullMinute + String(EncodernewPosition) + " Uhr" + "   ";

            DOG.string(0, 4, UBUNTUMONO_B_16, Value.c_str() , ALIGN_CENTER);
          }
          break;
        case 8:
        case 9: //Fahrtzeiteinstellung
          {
            Flashdaten.ontime = EncodernewPosition;




            String laufzeit = "     " + String(Flashdaten.ontime) + " s/10" + "     ";


            DOG.string(0, 4, UBUNTUMONO_B_16, laufzeit.c_str(), ALIGN_CENTER);

          }
          break;
        default:

          DOG.string(0, 4, UBUNTUMONO_B_16, "Default", ALIGN_CENTER);
          //dürfte nie eintreten!
          break;
      }

    }
    else if (menuposition > 9)
    {
      menuposition = 0;
      setEncoderPosition(menuposition);

    }
    else if (menuposition < 0)
    {
      menuposition = 8;
      setEncoderPosition(menuposition);

    }
  }

}


bool TimeCheck()
{
  bool a, b;

  int hour = Uhr.getHour(a, b);
  int minute = Uhr.getMinute();


  if (hour == Flashdaten.stundehoch && minute == Flashdaten.minutehoch)
  {
    handbetrieb = false;
    steuerunghoch();
  }

  if (hour == Flashdaten.stunderunter && minute == Flashdaten.minuterunter)
  {
    handbetrieb = false;
    steuerungrunter();
  }

}

bool Save()
{
  Flashspeicher.write(Flashdaten);
}

bool LoadValue()
{
  switch (menuposition)
  {
    case 0: //Status
    case 1:
      {


      }
      break;
    case 2: //Schließzeit
    case 3:
      {
        zwischenspeicherStunden = Flashdaten.stunderunter;
        zwischenspeicherMinuten = Flashdaten.minuterunter;
        setEncoderPosition(zwischenspeicherMinuten);
      }
      break;
    case 4: //Öffnenzeit
    case 5:
      {
        zwischenspeicherStunden = Flashdaten.stundehoch;
        zwischenspeicherMinuten = Flashdaten.minutehoch;
        setEncoderPosition(zwischenspeicherMinuten);
      }
      break;
    case 6: //Uhrzeit
    case 7:
      {
        bool a;
        bool b;
        zwischenspeicherUhrzeitStunden =   Uhr.getHour(a, b);
        zwischenspeicherUhrzeitMinuten = Uhr.getMinute();
        setEncoderPosition(zwischenspeicherUhrzeitMinuten);
      }
      break;
    case 8:
    case 9: //Fahrtzeit
      zwischenspeicherOnTime = Flashdaten.ontime;
      setEncoderPosition(zwischenspeicherOnTime);
      break;
    default:
      //dürfte nie eintreten!
      break;
  }
}

bool Handbetrieb ()
{


  if (btnState && !handstate)
  {

    up_down++;
    if (up_down > 5)
    { up_down = 0;
    }
    Serial.println(up_down);
    Serial.println(current_mA);
    switch (up_down)
    {
      case 0:
        HandRelaisOff();
        break;

      case 1:

        break;

      case 2:
        handbetrieb = true;
        steuerunghoch();
        break;

      case 3:
        HandRelaisOff();//fehler

        break;

      case 4:

        break;

      case 5:
        handbetrieb = true;
        steuerungrunter();
        break;
      default:

        break;
    }
  }

  handstate = btnState;

  //pressed = false;
  //Serial.println(handstate);
  return true;


}

bool UndervoltageCheck ()
{
  if (UBATValue < 110)
  {
    setFaultLED(10, 0, 0);
    return true;
  }
  else if (UBATValue > 135)
  {
    setFaultLED(0, 10, 0);
    return false;
  }
  else
  {
    setFaultLED(0, 0, 0);
    return false;
  }
}

bool checkEdge()
{

  if (!EndstopTop && lastcheck)
  {
    FallingEdge = true;
  }
  else
  {
    FallingEdge = false;
  }
  lastcheck = EndstopTop;

  return true;
}

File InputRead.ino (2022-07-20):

bool ReadEncoder ()
{
  EncodernewPosition = Drehencoder.read();
  //  Serial.println(EncodernewPosition);
  if (EncodernewPosition != EncoderoldPosition) {
    EncoderoldPosition = EncodernewPosition;
    displaytimer = true;
  }
  return true;
}

bool setEncoderPosition (long setEncoderPosition)
{
  Drehencoder.write(setEncoderPosition);
  //  Serial.println(EncodernewPosition);
  return true;
}

bool readEncoderBtn()
{
  int savemenuposition = 0;
  EncoderbtnState = !digitalRead(ENCODER_BTN);  //EncoderbtnState ist true wenn Taste gedrückt
  if ((millis() - lastDebounceTime) > debounceDelay)
  {
    if (EncoderbtnState && !EncoderbtnLastState) //wenn Button Gedrückt
    {
      if (EncoderbuttonToggle) //Menü wird verlassen
      {
        if (menuposition == 6 || menuposition == 7)
        {
          Uhr.setHour(stundeset);
          Uhr.setMinute(minuteset);
          setEncoderPosition(savemenuposition);
          Serial.println("Zeit gestellt");

        }
        else
        {
          setEncoderPosition(savemenuposition);
          Save();
          //Serial.println("Speichern");
        }

      }
      if (!EncoderbuttonToggle) //Menü wird geöffnet
      {
        savemenuposition = menuposition;
        LoadValue();

      }
      EncoderbuttonToggle = !EncoderbuttonToggle;
      lastDebounceTime = millis();
      displaytimer = true;
    }
    EncoderbtnLastState = EncoderbtnState;
  }
  return true;
}

bool readBtn()
{
  btnState = !digitalRead(USER_BTN);
  return true;
}

bool readEndstopTop()
{
  EndstopTop = digitalRead(ENDSTOP_TOP);

  return true;
}

bool readEndstopBottom()
{
  EndstopBottom = digitalRead(ENDSTOP_BOTTOM);
  return true;
}

bool readNOTAUS()
{
  NOTAUSstate = !digitalRead(NOTAUS);
  return true;
}

bool readPotiValue ()
{
  int WerteSumme = 0;
  int AnzahlSamples = 32;
  for (int i = 0; i < AnzahlSamples; i++)
  {
    WerteSumme = WerteSumme + SENSITIVITY;

  }
  PotiValue = WerteSumme / AnzahlSamples;

  return true;
}

bool readLDRValue ()
{
  int WerteSumme = 0;
  int unmappedLDRValue = 0;
  int AnzahlSamples = 120;
  for (int i = 0; i < AnzahlSamples; i++)
  {
    WerteSumme = WerteSumme + analogRead(LDR);

  }
  unmappedLDRValue = WerteSumme / AnzahlSamples;
  LDRValue = map(unmappedLDRValue, 500, 1023, 0, 1023);
  return true;
}

bool readUbat ()
{
  float WerteSumme = 0;
  float unmappedUbatValue = 0;
  int AnzahlSamples = 50;
  for (int i = 0; i < AnzahlSamples; i++)
  {
    WerteSumme = WerteSumme + UBAT;

  }
  unmappedUbatValue = WerteSumme / AnzahlSamples;
  UBATValue = (unmappedUbatValue - 0) * (250 - 0) / (2.28 - 0) + 0;
  return true;
}

bool readINA()
{



  current_mA = ina219.getCurrent_mA();
  //Serial.print("Current:       "); Serial.print(current_mA); Serial.println(" mA");


  return true;
}

bool readADC()
{
  UBAT = readChannel(ADS1115_COMP_0_GND);
  USOLAR = readChannel(ADS1115_COMP_1_GND);
  SENSITIVITY = readChannel(ADS1115_COMP_2_GND);
}

float readChannel(ADS1115_MUX channel) {
  float voltage = 0.0;
  adc.setCompareChannels(channel);
  voltage = adc.getResult_V(); // alternative: getResult_mV for Millivolt
  return voltage;
}

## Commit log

2022-07-20 PCB Files hinzugefügt
    [Steuerung.brd, Steuerung.csv, Steuerung.sch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]
2022-07-21 Release 20.7.
    Überstrom & NOTAUS Abschaltung deaktiviert (Hat Probleme bereitet)
    [Chicken_Coop.ino, Outputs.ino]

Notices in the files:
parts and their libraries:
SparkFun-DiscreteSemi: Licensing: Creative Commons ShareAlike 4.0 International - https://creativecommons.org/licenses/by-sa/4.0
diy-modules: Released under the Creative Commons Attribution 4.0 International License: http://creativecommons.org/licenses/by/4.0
